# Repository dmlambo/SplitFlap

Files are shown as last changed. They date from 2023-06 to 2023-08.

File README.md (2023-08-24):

# SplitFlap

ESP8266 based controller for split flap display modules. The code is all-in-one, meaning each module runs the same code, but in different modes set in EEPROM. The master runs the web server and controls the first unit, and each other unit acts as an I2C slave to control its own unipolar stepper motor.

## Video!

Splitflap Display in Action! (https://www.youtube.com/watch?v=YFdsrr4tarE)

## Attribution
This design is mostly [David Königsmann's fantastic design](https://github.com/Dave19171/split-flap) with changes to improve printability, improve durability, or reduce filament use. Specifically the unit has been reduced to 8 characters so it could be printed on an Ender 3 V2. That said, most of the changes are just personal preference, and hats off to David for his great design.

## Electronics
The name of the game is low-cost, and ease of construction. Not that David's design isn't already low cost, but I am a cheapskate. Each module's BOM is very low, making use of the ULN2003 that you usually get with your 28BYJ-48 steppers (as with David's) but instead of having an Arduino Nano for each, along with an ESP01, each module only uses a single ultra-cheap Wemos Lolin D1 Mini V4 (any version with the ESP8266EX, without the metal sheild, will work). The rest is just support components, and everything is through-hole mounted. 

## Software
The main difference between the two projects is in the software. Since David's module was split into two MCUs, on two different architectures, he had to maintain two different codebases. Therefore I chose to unify mine, not just for ease of programming (and debugging) but also easy of maintenance. Since everything is software controlled, including the I2C address, one only has to connect to Serial over USB on the master, or on the unit itself, to change any running parameters they want. 
Similarly, the web interface does a few things for you. There is a frontend to change what's displayed, and to change, for example, the timezone and date formating. However, there is also a RESTful API available if someone wanted to make their own front end.
Finally, indeed the software uses the Arduino platform code, but rather than being an Arduino project, it is a PlatformIO project. This was important for organization, since the way Arudino mangles up your code means compartmentalizing is often impossible.

## Wire implementation
The ESP8266 core has a bad I2C implementation. I've patched it up manually to keep it from doing weird things, and destabilizing the system, such as doing clock stretching in odd places, or setting SDA low/high immediately before or after toggling SCL. I've also enabled GCALL by means of always responding ACK to address 0. It seems to work, but it is certainly being misused. 

## Building Notes
The master device needs 2 4.7k pullup resistors on 4 and 5, that is, SDA and SCL. The hall sensor output also has to be rerouted to D0, and a 10k pullup should be added, since D0 does not have one internally. These features have not beed added to the schematic or the PCB, so if you build this as-is, expect a bit of manual work.

## FAQ
### How do I disconnect my display from the network?
There's a reset button on the left side. Press it three times. This should clear your credentials.

### How do I update my firmware/filesystem?
Go to http://splitflap.local/update.html and put your firmware.bin/littlefs.bin file into the form and press submit. Wait about 30 seconds, or until the form times out. Do not reset your device until you regain contact with it through the web portal, or you might interrupt the update sequence.

### I flashed a new firmware that had a change to the Config structure, and now my display isn't responding
There's a reset button on the left side. Press it six times. This should toggle the master mode.

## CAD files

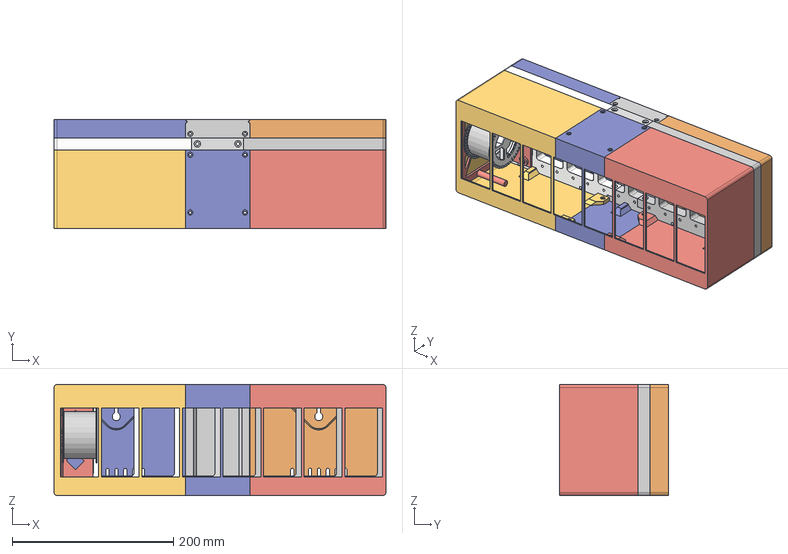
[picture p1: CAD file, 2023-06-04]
models/AssemblyWithChanges.step
412.4 x 135.8 x 138.0 mm
BigRotor
MiniRotor
Frame
HousingFrame
FrameBack
FrameFront

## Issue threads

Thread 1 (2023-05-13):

[Hardware] PCB issues

dmlambo, 2023-05-13:
Reroute D3 to D0, add pullup on D0, maybe swap polarity on 12V harnesses?

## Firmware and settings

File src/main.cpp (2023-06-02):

#include <Arduino.h>

#include <Wire.h>
#include <EEPROM.h>
#include <LittleFS.h>

//#include <ESPAsyncWebServer.h>
#include <WiFiManager.h>
#include <ESP8266TrueRandom.h>

#include "Config.h"
#include "Commands.h"
#include "Communication.h"
#include "Display.h"
#include "Motor.h"
#include "WebServer.h"
#include "Utils.h"

#include <ESP8266mDNS.h>
#include <flash_hal.h>

#include <lwip/tcp.h>

#include <ESPAsyncTCP.h>

// Default config
ModuleConfig Config = { 
  .magic = CONFIG_MAGIC + sizeof(ModuleConfig), 
  .isMaster = 0, 
  .address = 0, 
  .zeroOffset = 0,
  .rpm = 15, 
  .multilineDelay = 6000,
  .timeZone = { 0 },
};

void setup() {
  bool firstBoot = true; 

  pinMode(MOTOR_IN1, OUTPUT);
  pinMode(MOTOR_IN2, OUTPUT);
  pinMode(MOTOR_IN3, OUTPUT);
  pinMode(MOTOR_IN4, OUTPUT);

  digitalWrite(MOTOR_IN1, 0);
  digitalWrite(MOTOR_IN2, 0);
  digitalWrite(MOTOR_IN3, 0);
  digitalWrite(MOTOR_IN4, 0);

  // D0 *DOES NOT* have a pullup.
  pinMode(HALL, INPUT_PULLUP);

  // It's somewhat important where this goes, since we rely on reset timing to determine whether to forget WiFi or become the master
  unsigned int resetCount = countResets();

  Serial.begin(57600);

  while (!Serial) { yield(); }

  LOGLN();
  LOGLN("Welcome to Dave's Split Flap Experience!");

  // Debug.. 
  delay(2000); 

  if(!LittleFS.begin()){
    LOGLN("An Error has occurred while mounting LittleFS");
    return;
  }

  EEPROM.begin(sizeof(ModuleConfig));

  // Valid saved config
  if (((unsigned int *)EEPROM.getConstDataPtr())[0] == CONFIG_MAGIC + sizeof(ModuleConfig)) {
    firstBoot = false;
    memcpy(&Config, EEPROM.getConstDataPtr(), sizeof(ModuleConfig));

    LOGLN("Active configuration loaded from flash");
  } else {
    // First bootup
    LOGLN("First time boot or config size mismatch, using defaults");
  }

  printConfig(&Serial);

  LOGLN();

  printCommandHelp(&Serial);

  // On first flash, we start in slave mode, but as a master I2C device. We wait a random amount of time
  // and try to assign our random address by first requesting data from said address. If no one responds
  // we keep it, if someone responds we move onto another address. Once we find an empty address, we 
  // write the config and reboot. However, we need to give other modules a time to do this entire
  // song and dance, so that we ensure we take control of the bus at some point (there's no arbitration)
  // and give others a chance to assign their own address and reboot into slave mode.
  if (firstBoot) {
    LOG("Searching for unused I2C address between " DEFTOLIT(I2C_DEVADDR_MIN+DISPLAY_MAX_MODULES) " and " DEFTOLIT(I2C_DEVADDR_MAX));

    Wire.begin();

    Config.address = ESP8266TrueRandom.random(I2C_DEVADDR_MIN+DISPLAY_MAX_MODULES, I2C_DEVADDR_MAX);

    bool addrFound = false;
    int attempts = 100;

    while (!addrFound && attempts--) { 
      ModuleStatus status;
      delayMicroseconds(ESP8266TrueRandom.random(0, 40000));
      if (i2cReadStruct(Config.address, &status) == PACKET_OK) {
        LOG("Found module at address "); LOGLN((int)Config.address);
        attempts = 100;
        Config.address = ESP8266TrueRandom.random(I2C_DEVADDR_MIN+32, I2C_DEVADDR_MAX);
      }
    }

    LOG("Found unused address "); LOGLN((int)Config.address);
    saveConfig();
    LOGLN("Rebooting...");
    Serial.flush();
    ESP.reset();
  }

  LOG("Reset count: "); LOGLN(resetCount);
  if (resetCount > 1) {
    if (resetCount >= RESET_BECOME_MASTER) {
      LOGLN("Reset " DEFTOLIT(RESET_BECOME_MASTER) " times, becoming master");
      Config.isMaster = true;
      saveConfig();
    }
  }

  motorInit();

  if (Config.isMaster) {
    LOGLN("Starting in master mode.");

    Wire.begin();
    Wire.setClock(I2C_FREQUENCY);
    Wire.setClockStretchLimit(40000);

    // Find all other devices
    enumerateModules();

    {
      WiFiManager wifiManager;

      wifiManager.setAPCallback([] (WiFiManager *myWiFiManager) {
        displayMessage("USE AP", sizeof("USE AP")-1, 0, 0, JustifyCenter);
        displayEvents(); // Normally done in loop
      });

      if (resetCount >= RESET_WIFI_COUNT) { 
        LOGLN("WiFi credentials reset due to external button sequence");
        wifiManager.resetSettings();
      }

      LOGLN("Connecting to WiFi...");
      WiFi.setHostname(WIFI_HOSTNAME);
      while (!wifiManager.autoConnect(WIFI_AP_NAME)) {
        LOGLN("Failed to connect to network. Retrying.");
      }
      LOGLN("Success!");
      displayMessage(" ", 1); // Calibrate
    }

    delay(1000);

    tcpCleanup();

    // Not sure if needed, but we should probably wait for lwip's fast and slow timer procs to run (250/500ms)
    delay(1000);;

    if (!MDNS.begin(WIFI_MDNS_HOSTNAME)) {
      LOGLN("Failed to create MDNS responder");
    }

    LOGLN("Initializing web server");
    WebServerInit();

    MDNS.addService("http", "tcp", 80);
    
    LOG("Found "); LOG(nKnownModules); LOGLN(" other I2C devices.");
  } else {
      LOG("Starting in slave mode at address "); LOGLN((int)Config.address);
      Wire.begin(Config.address);
      pinMode(SDA, INPUT); // Turn off pullups
      pinMode(SCL, INPUT); 
      Wire.setClock(I2C_FREQUENCY);
      Wire.setClockStretchLimit(40000);
      Wire.onRequest(onRequestI2C);
      Wire.onReceive(onReceiveI2C);
  }
}

void loop() {
  // Handle immediate events
  if (Serial.available()) {
    char commandBuff[128];
    commandBuff[Serial.readBytesUntil('\0', commandBuff, sizeof(commandBuff))] = 0;
    handleCommand(commandBuff, &Serial);
  }

  char* i2cCommand = i2cReadCommand();

  if (i2cCommand && *i2cCommand) {
    //LOGLN("Reveived I2C command...");
    handleCommand(i2cCommand, &Serial);
  }

  if (queuedCommand.queued && !queuedCommand.finished) {
    handleCommand(queuedCommand.params); // TODO: Percolate error to caller
    queuedCommand.finished = true; // mark as done
  }

  if (i2cOverflow) {
    deviceLastStatus = MODULE_OVERFLOW;
    i2cOverflow = false;
    LOGLN("I2C command buffer overflow.");
  }

  if (motorCalibrated) {
    motorCalibrated = false;
    LOGLN("Motor is calibrated.");
  }

  if (motorStalled) {
    motorStalled = false;
    LOGLN("Motor stalled.");
  }
  // ~immediate events

  // When in master mode, we run extra services; the http server, mDNS, time, etc.
  if (Config.isMaster) {
    MDNS.update();
    displayEvents();
  }

  if (shouldReboot()) {
    ESP.restart();
  }
}

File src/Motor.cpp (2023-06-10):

#include <Arduino.h>

#include "Config.h"

#include "Communication.h"
#include "Motor.h"

const bool PinStates[][4] = {
  { true, false, false, false },
  { false, false, false, true },
  { false, false, true, false },
  { false, true, false, false },
};

const char Pins[] = { MOTOR_IN1, MOTOR_IN2, MOTOR_IN3, MOTOR_IN4 };

static unsigned char motorState = 0;

// These are separated into two variables since the timer interrupt runs constantly, and we don't ever want to skip a step
// if we enable the motor too soon before the next interrupt, by, for instance, setting another target mid-turn
static volatile bool motorEnabled = false;
static volatile bool motorRunning = false;
static volatile int motorStep = -MOTOR_STEPS; // This gives it a chance to calibrate on start
static volatile int motorTarget = 0;
static volatile unsigned int motorHold = MOTOR_HOLD;
static volatile int hallDebounce = 0;
static volatile int waitForLow = false;
static volatile unsigned int currentFlap = MOTOR_FLAPS; // Start out of range

volatile bool motorCalibrated = false;
volatile bool motorStalled = false;

void IRAM_ATTR doMotorISR(void *para, void *frame) {
  if ((T1C & ((1 << TCAR) | (1 << TCIT))) == 0) TEIE &= ~TEIE1;//edge int disable
  T1I = 0;
  if (motorEnabled) {
    if (deviceLastStatus != MODULE_CALIBRATING) deviceLastStatus = MODULE_MOVING;
    if (motorRunning) {
      // Since we subtract the zero offset, the last flap may actually be in between the zero point and true zero, where motorStep is negative
      // Furthermore, there's no difference between a target of 0 and calibration, and we calibrate every time we pass the hall
      if ((motorTarget == 0 && motorStep == 0) || 
          (motorTarget != 0 && (motorStep == motorTarget || motorStep + MOTOR_STEPS == motorTarget))) {
        motorRunning = motorEnabled = false;
        deviceLastStatus = MODULE_OK;
      } else {
        motorState++;
        motorState %= 4;
        motorStep++;

        if (motorStep >= MOTOR_STEPS + MOTOR_STALL_STEPS) { // Done a whole rotation without seeing the hall sensor. We've stalled.
          deviceLastStatus = MODULE_STALLED;
          motorStalled = true;
          motorRunning = motorEnabled = false;
          motorHold = 0;
          motorStep = 0;
        }
      }
    } else {
      // Advance the next time around
      motorRunning = true;
      motorHold = MOTOR_HOLD;
    }
    digitalWrite(Pins[0], PinStates[motorState][0]);
    digitalWrite(Pins[1], PinStates[motorState][1]);
    digitalWrite(Pins[2], PinStates[motorState][2]);
    digitalWrite(Pins[3], PinStates[motorState][3]);
  } else {
    if (motorHold) {
      motorHold--;
    } else {
      digitalWrite(Pins[0], false);
      digitalWrite(Pins[1], false);
      digitalWrite(Pins[2], false);
      digitalWrite(Pins[3], false);
      disableMotorTimer();
    }
  }

  if (!digitalRead(HALL)) {
    hallDebounce++;
  } else {
    hallDebounce--;
  }

  if (hallDebounce > HALL_DEBOUNCE) {
    hallDebounce = HALL_DEBOUNCE;
    // At startup, even if we're next to the hall sensor, we'll need to go around again
    if (!waitForLow) {
      motorStep = -Config.zeroOffset;
      motorCalibrated = true;
      waitForLow = true;
    }
  }
  if (hallDebounce < 0) {
    waitForLow = false;
    hallDebounce = 0;
  }
}

void motorCalibrate() {
  LOGLN("Calibrating...");
  deviceLastStatus = MODULE_CALIBRATING;

  noInterrupts();
  motorStep = 1;
  motorTarget = 0;
  motorEnabled = true;
  motorCalibrated = false;
  waitForLow = !digitalRead(HALL);
  hallDebounce = waitForLow ? HALL_DEBOUNCE : 0;
  interrupts();
  enableMotorTimer();
}

void motorSetRPM(int rpm) {
  float usecPerRev = (float)(1000000 * 60) / (float)rpm;
  float usecPerStep = usecPerRev / (float)MOTOR_STEPS;
  int timerValue = CPU_CLK_FREQ / 16 / 1000000 * usecPerStep;

  timer1_write(timerValue);
}

void motorMoveToFlap(unsigned int flap) {
  // Require a calibrate after a stall
  if (deviceLastStatus == MODULE_STALLED) return;

  // No work to be done
  if (flap == currentFlap) return;

  if (flap >= MOTOR_FLAPS) {
    flap = 0;
  }

  currentFlap = flap;

  noInterrupts();
  motorTarget = (int)((float)flap * ((float)MOTOR_STEPS / (float)MOTOR_FLAPS));
  motorEnabled = true;
  interrupts();
  enableMotorTimer();
}

unsigned int motorCurrentFlap() {
  return currentFlap;
}

void motorInit() {
  disableMotorTimer();
  // Subvert the Arduino core ISR, since it disables interrupts, which messes up flash.
  //timer1_attachInterrupt(doMotorISR); <- no!
  ETS_FRC_TIMER1_INTR_ATTACH(doMotorISR, NULL);
  ETS_FRC1_INTR_ENABLE();
  motorSetRPM(Config.rpm);
  //enableMotorTimer();
}

void disableMotorTimer() {
  timer1_disable();
}

void enableMotorTimer() {
  timer1_enable(TIM_DIV16, TIM_EDGE, TIM_LOOP);
}

void motorDebugPrint() {
  static int i = 0;
  if (!(i++ % 1000)) {
    LOGLN(motorStep);
  }
}

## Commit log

2023-05-08 Remove original Arduino main
2023-05-08 Remove original Arduino main, but for real.
2023-05-08 Add half-step motor implementation, change D3 to D0 for hall (oops), add motor calibration code
2023-05-09 Add speed command and config storage. Fix bug where clearing flash crashes the device due to motor poll routine.
    [Commands.cpp, Motor.cpp, main.cpp]
2023-05-12 Add time/date display, ephemeral (temporary) message display, NTP time updating, time zone storage in flash, and automatic i2c address resolution.
2023-05-13 Wire module needs callback or available() returns 0.
2023-05-21 Add WiFi credential reset procedure. Fix bug with first start AP not properly closing established TCP sockets.
    [Commands.cpp, Display.cpp, Motor.cpp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]
2023-05-24 Add cmd endpoint to run all Serial commands from a browser. Remove charmap from Config. Fix RTC reset count, and add master mode with 6 reset clicks.
    [Commands.cpp, WebServer.cpp]
2023-05-28 Make command handling async for the webserver, don't disable interrupts for the motor ISR, move to full stepping
2023-06-04 Add step for the assembly, and the PCB in EasyEDA format.
    [AssemblyWithChanges.step]
2023-06-09 Fix bug with justify
    [Display.cpp]
